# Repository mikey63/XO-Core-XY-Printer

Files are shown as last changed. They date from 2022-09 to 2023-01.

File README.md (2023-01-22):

# XO-Core-XY-Printer
Compact Enclosed Core XY 3D printer with design elements from multiple open-source printers
This printer is based on the Voron V.0, Tiny M, and SnakeOil XY printers.  It's basically a larger version of a Voron V.0 using 2020 extrusions, and has a 220x220x200 build volume, but the electronics setup from a Trident.

Uses BTT Octopus for MCU, and a Raspberry Pi for Klipper.

Use the Voron Trident documentation to setup the MCU and Klipper, then use my config and klicky files.  That should get you up and running, and nearly ready to print.  Before printing, make sure to fine tune the clicky dock position.

For more info:
https://www.youtube.com/watch?v=fIn6DrubGhQ

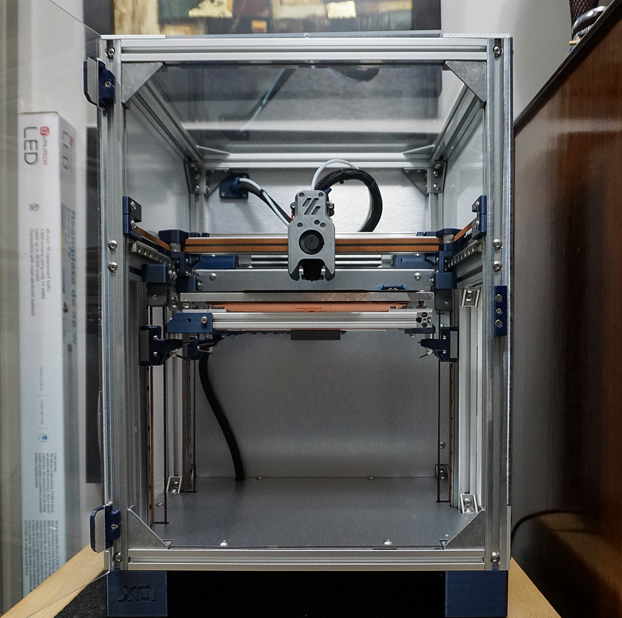
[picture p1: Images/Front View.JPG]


# NOTES

# ***UPDATE 1/21/23!!***

A.  NEW Toolhead!  I am in the process of upgrading to the new Voron V0.2 Mini Stealthburner toolhead!  Of course, I modified it to work with the longer Rapido hotend.  The basic toolhead parts are the same as the voron version, and I changed up the X carriage to match the new bolt pattern.  This means that any V0.2 toolhead will bolt on the carrage, no modified parts are needed like before.  Hopefully, this makes it easier to use the stock voron toolhead, or any iteration meant to work with the voron 0.2 carriage mount.  The Voron team did a great design on this new version, so I removed the original mini-afterburner from the model.  The only changed part on my stealthburner version is the front shroud, and the Rapido hotend mount.  Now that the hotend mount is a separate part, it makes it much easier to assemble, and change hotends!

B. Minor corrections to the CAD model were made.  notably one of the rear bed carrier brackets, and the Z carriage bearing hole was made a tiny bit smaller in hopes for a tighter fit.  

Other than that, there hasn't been much development.  Mostly because the printer has been amazing, and I haven't run into any issues that needed to be addressed.

PREVIOUS NOTES BELOW:

1.  I'm still working on a composite BOM for the major components (like frame parts).  I did not render every fastener, screw, bolt, etc.  I learned fusion360 as a hobby, and just didn't have the time and skill for a professional rendor like that (sorry!)
2.  That said - you will need a few packs of M5 bolts (I used button head M5's), and also some M3 (socket head) bolts.  Also get the corresponding M5 and M3 drop-in T-nuts.  I don't have the exact count on these since I had multiple packs in my stash that I picked from.  Typical M5 variety packs should work, but you may need to get a pack of Just longer M5's, from 20mm-40mm for the few longer pieces you will need.  you'll also need a few 3mm square nuts for the x carriage mount.
3.  I'm using 20x40mm corner gussets from Framingtech.com https://www.framingtech.com/20-x-40-gusset at the inside corners of the frame. These are pretty pricey, but they are very well made.  You can substitute these with some regular corner brackets if you want to save some money.
4.  for motors - X and Y can use any typical Nema 17.  I used 48mm Motors.  For the Z motors, you will need to use the pre-geared Nema 17s, like these: https://www.amazon.com/gp/product/B00WATUFIG/ref=ppx_yo_dt_b_search_asin_title?ie=UTF8&psc=1   These steppers have a built in 5.18:1 gear ratio.  The config file will have the correct rotation distance in the Z_stepper section for these to work.  The Toolhead uses a 36mm round Nema 14 that is typical to other small extruders, like the orbiter or mini-sherpa.
5.  The tool head is a modified V0 tool head.  it has longer fan ducts for a rapido hotend, and it's 3mm thicker on the front side to account for a 30x30x10mm fan in lieu of a 30x30x7mm fan that is the standard for the V0.  You can use the stock V0 in it's place, or any one of the other iterations and mods for this toolhead.
6.  The X carriage is a little different than the standard voron carriage, as it has accomodations for the clicky probe mount, and also a custom backplate behind the nema motor for wire management.  These extra parts can be easily modified to account for different hotends and wiring setups.  right now most of the parts have captured nuts, but I will be working on a version with heatset inserts for a future update.  Some of the captured nuts I'm using at the sides of the mount are 3mm square nuts.  again, this may be updated to heat inserts sometime in the future, when I get around to buying some more.
7.  The bed frame uses 1515 extrusions and matching corner brackets that I had custom laser cut.  There is a dxf file for these triangular brackets that you can send to a 3rd party laser cutting service to have made.  I had them made at the same time I had the side panels cut, and used SendCutSend, located in the USA.  You can probably aso 3d print these parts as well.
8.  This IS a work in progress for the most part.  If you find any issues, or have questions, please let me know, and I'll do my best to update the files.

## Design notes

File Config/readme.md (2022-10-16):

To setup your klicky probe, make a directory in your Klipper "config" folder called "klicky" Then copy these files into that folder. be sure to check out klicky documentation for more information: https://github.com/jlas1/Klicky-Probe

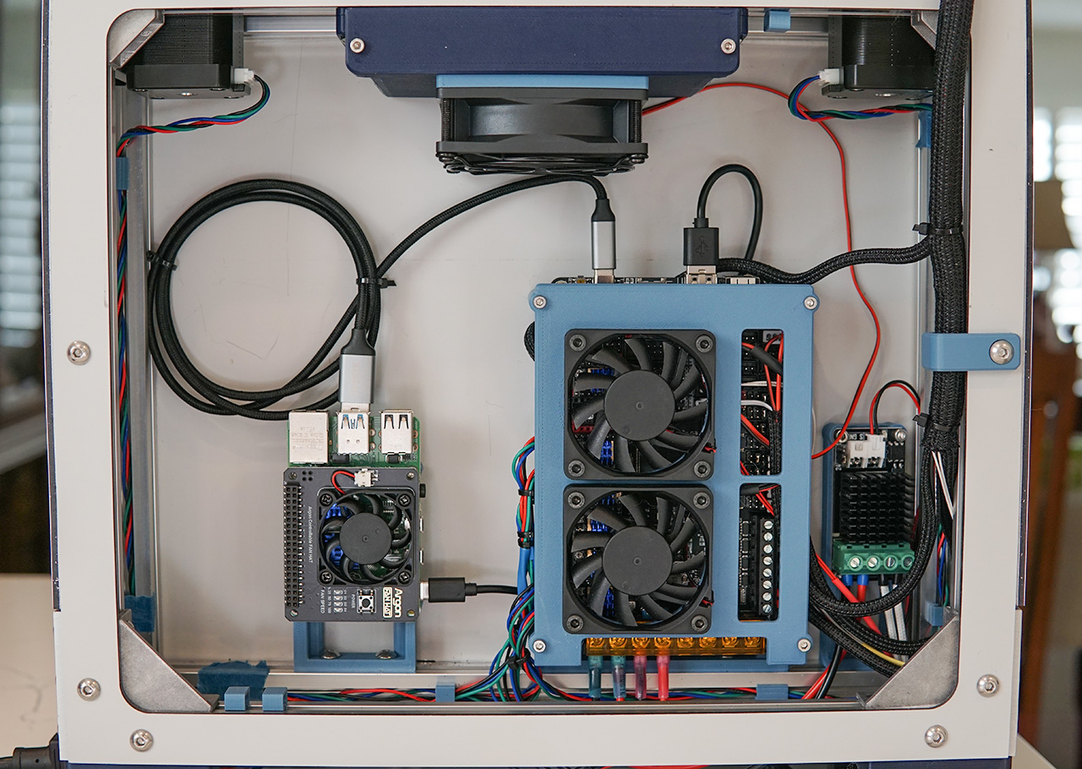
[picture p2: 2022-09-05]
Images/Rear Panel Electronics.JPG

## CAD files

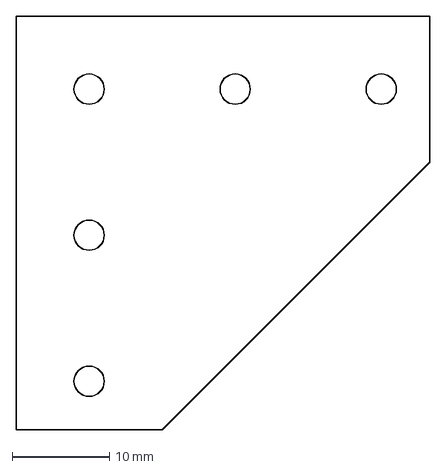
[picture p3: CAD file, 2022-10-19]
CAD Assembly/1515 Corner Plate for Bed Frame.dxf
42.5 x 42.5 mm

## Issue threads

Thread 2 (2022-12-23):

[Suggestion] Control your RPI fan hat with macros

thiagolocatelli, 2022-12-23:
You can control the fan speed on your fan hat by using macros and I2C. Just install the gcode shell command klipper plugin (manually or via Kiuah), enable I2C via `raspi-config` and then use there

```
[gcode_shell_command rpi_fan_50]
command: i2cset -y 1 0x01a 0x32
timeout: 30.
verbose: True

[gcode_shell_command rpi_fan_25]
command: i2cset -y 1 0x01a 0x19
timeout: 30.
verbose: True

[gcode_macro rpi_fan_50]
gcode:
    RUN_SHELL_COMMAND CMD=rpi_fan_50

[gcode_macro rpi_fan_25]
gcode:
    RUN_SHELL_COMMAND CMD=rpi_fan_25
```

mikey63, 2022-12-23:
Awesome, Thank you!  I'll give this a shot.

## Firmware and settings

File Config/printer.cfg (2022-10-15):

# This file contains common pin mappings for the BigTreeTech Octopus V1.
# To use this config, the firmware should be compiled for the STM32F446 with a "32KiB bootloader"
# Enable "extra low-level configuration options" and select the "12MHz crystal" as clock reference

# after running "make", copy the generated "klipper/out/klipper.bin" file to a
# file named "firmware.bin" on an SD card and then restart the OctoPus with that SD card.

# See docs/Config_Reference.md for a description of parameters.

## Voron Design Trident 250/300/350mm BigTreeTech OctoPus V1 TMC2209 UART config

## *** THINGS TO CHANGE/CHECK: ***
## MCU paths                            [mcu] section
## Thermistor types                     [extruder] and [heater_bed] sections - See https://www.klipper3d.org/Config_Reference.html#common-thermistors for common thermistor types
## Leadscrew Rotation Distance          [stepper_z], [stepper_z1], [stepper_z2]
## Z Endstop Switch location            [safe_z_home] section
## Z Endstop Switch  offset for Z0      [stepper_z] section
## PID tune                             [extruder] and [heater_bed] sections
## Probe pin                            [probe] section
## Fine tune E steps                    [extruder] section


[mcu]
##  Obtain definition by "ls -l /dev/serial/by-id/" then unplug to verify
##--------------------------------------------------------------------
serial: /dev/serial/by-id/usb-Klipper_stm32f446xx_370021000F5053424E363620-if00
restart_method: command
##--------------------------------------------------------------------


[include mainsail.cfg]
[include klicky/klicky-probe.cfg]


[printer]
kinematics: corexy
max_velocity: 400 
max_accel: 8000             #Max 4000
max_z_velocity: 18          #Max 15 for 12V TMC Drivers, can increase for 24V
max_z_accel: 350
square_corner_velocity: 5.0

[firmware_retraction]
retract_length: 1.2
retract_speed: 55
unretract_extra_length: 0
unretract_speed: 45

#####################################################################
#   X/Y Stepper Settings
#####################################################################

##  B Stepper - Left
##  Connected to MOTOR_0
##  Endstop connected to DIAG_0
[stepper_x]
step_pin: PF13
dir_pin: PF12
enable_pin: !PF14
rotation_distance: 40
microsteps: 32
full_steps_per_rotation: 200  #set to 400 for 0.9 degree stepper
#endstop_pin: PG6   #Not needed for sensorless homing?
endstop_pin: tmc2209_stepper_x:virtual_endstop
#position_min: 0    #Not needed for sensorless homing?
position_max: 210
position_endstop: 0
##--------------------------------------------------------------------
homing_speed: 90      #Max 100
homing_retract_dist: 0
homing_positive_dir: false

##  Make sure to update below for your relevant driver (2208 or 2209)
[tmc2209 stepper_x]
uart_pin: PC4
diag_pin: ^PG6
interpolate: False
run_current: 1.0
sense_resistor: 0.110
stealthchop_threshold: 0
driver_SGTHRS:  115

##  A Stepper - Right
##  Connected to MOTOR_1
##  Endstop connected to DIAG_1
[stepper_y]
step_pin: PG0
dir_pin: PG1
enable_pin: !PF15
rotation_distance: 40
microsteps: 32
full_steps_per_rotation: 200  #set to 400 for 0.9 degree stepper
#endstop_pin: PG9
endstop_pin: tmc2209_stepper_y:virtual_endstop
#position_min: 0
position_max: 229
position_endstop: 0
##--------------------------------------------------------------------
homing_speed: 90  #Max 100
homing_retract_dist: 0
homing_positive_dir: false

##  Make sure to update below for your relevant driver (2208 or 2209)
[tmc2209 stepper_y]
uart_pin: PD11
diag_pin: ^PG9
interpolate: False
run_current: 1.0
sense_resistor: 0.110
stealthchop_threshold: 0
driver_SGTHRS:  115
 
#####################################################################
#   Z Stepper Settings
#####################################################################

##  Z0 Stepper - Front Left
##  Connected to MOTOR_2
##  Endstop connected to DIAG_2
[stepper_z]
step_pin: PF11
dir_pin: PG3
enable_pin: !PG5
# Rotation Distance for TR8x8 = 8, TR8x4 = 4, TR8x2 = 2
rotation_distance: 7.75    
microsteps: 32
#endstop_pin: PG10
endstop_pin: probe:z_virtual_endstop
##  Z-position of nozzle (in mm) to z-endstop trigger point relative to print surface (Z0)
##  (+) value = endstop above Z0, (-) value = endstop below
##  Increasing position_endstop brings nozzle closer to the bed
##  After you run Z_ENDSTOP_CALIBRATE, position_endstop will be stored at the very end of your config
#position_endstop: 0.125
## All builds use same Max Z
position_max: 190
position_min: -2.5
homing_speed: 11.0 # Leadscrews are slower than 2.4, 10 is a recommended max.
second_homing_speed: 3
homing_retract_dist: 3

##  Make sure to update below for your relevant driver (2208 or 2209)
[tmc2209 stepper_z]
uart_pin: PC6
interpolate: False
run_current: 0.6
sense_resistor: 0.110
stealthchop_threshold: 999

##  Z1 Stepper - Rear Center
##  Connected to MOTOR_3
[stepper_z1]
step_pin: PG4
dir_pin: PC1
enable_pin: !PA0
# Rotation Distance for TR8x8 = 8, TR8x4 = 4, TR8x2 = 2
rotation_distance: 7.75
microsteps: 32

##  Make sure to update below for your relevant driver (2208 or 2209)
[tmc2209 stepper_z1]
uart_pin: PC7
interpolate: False
run_current: 0.6
sense_resistor: 0.110
stealthchop_threshold: 999

##  Z2 Stepper - Front Right
##  Connected to MOTOR_4
[stepper_z2]
step_pin: PF9
dir_pin: PF10
enable_pin: !PG2
# Rotation Distance for TR8x8 = 8, TR8x4 = 4, TR8x2 = 2
rotation_distance: 7.75 
microsteps: 32

##  Make sure to update below for your relevant driver (2208 or 2209)
[tmc2209 stepper_z2]
uart_pin: PF2
interpolate: False
run_current: 0.6
sense_resistor: 0.110
stealthchop_threshold: 999


#####################################################################
#   Extruder
#####################################################################

#   Connected to MOTOR_6
#   Heater - HE0
#   Thermistor - T0
[extruder]
step_pin: PE2
dir_pin: !PE3
enable_pin: !PD4
##  Update value below when you perform extruder calibration
##  If you ask for 100mm of filament, but in reality it is 98mm:
##  rotation_distance = <previous_rotation_distance> * <actual_extrude_distance> / 100
rotation_distance: 4.59   #Bondtech 5mm Drive Gears
##  Update Gear Ratio depending on your Extruder Type
##  Use 50:17 for Afterburner/Clockwork (BMG Gear Ratio)
##  Use 80:20 for M4, M3.1
#gear_ratio: 50:10               #mini afterburner/mini sherpa gear ratio
microsteps: 32
full_steps_per_rotation: 200    #200 for 1.8 degree, 400 for 0.9 degree
nozzle_diameter: 0.400
filament_diameter: 1.75
heater_pin: PA2
## Check what thermistor type you have. See https://www.klipper3d.org/Config_Reference.html#common-thermistors for common thermistor types.
## Use "Generic 3950" for NTC 100k 3950 thermistors
sensor_type: Generic 3950
sensor_pin: PF4
min_temp: 10
max_temp: 275
max_power: 1.0
min_extrude_temp: 170
#control = pid
#pid_kp = 26.213
#pid_ki = 1.304
#pid_kd = 131.721

max_extrude_only_distance: 500.0
#Maximum length (in mm of raw filament) that a retraction or extrude-only move may have. 
#If a retraction or extrude-only move requests a distance greater than this value it will 
#cause an error to be returned. The default is 50mm.

##  Try to keep pressure_advance below 1.0
pressure_advance: 0.040
##  Default is 0.040, leave stock
pressure_advance_smooth_time: 0.040

##  E0 on MOTOR6
##  Make sure to update below for your relevant driver (2208 or 2209)
[tmc2209 extruder]
uart_pin: PE1
interpolate: false
run_current: 0.50
sense_resistor: 0.110
stealthchop_threshold: 0


#####################################################################
#   Bed Heater
#####################################################################

[heater_bed]
##  SSR Pin - HE1
##  Thermistor - TB
heater_pin: PA3
## Check what thermistor type you have. See https://www.klipper3d.org/Config_Reference.html#common-thermistors for common thermistor types.
## Use "Generic 3950" for Keenovo heaters
sensor_type: Generic 3950
sensor_pin: PF3
##  Adjust Max Power so your heater doesn't warp your bed. Rule of thumb is 0.4 watts / cm^2 .
max_power: 0.6
min_temp: 0
max_temp: 120
#control: pid
#pid_kp: 58.437
#pid_ki: 2.347
#pid_kd: 363.769

#####################################################################
#   Chamber Temperature Monitoring
#####################################################################

#Not needed if chamber fan is configured below
[temperature_sensor chamber]
sensor_type: Generic 3950
sensor_pin: PF5
min_temp: 0
max_temp: 80
gcode_id: C

#####################################################################
#   Fan and Temperature Control
#####################################################################

[fan]
##  Print Cooling Fan - FAN0
pin: PA8
kick_start_time: 1.0
##  Depending on your fan, you may need to increase this value
##  if your fan will not start. Can change cycle_time (increase)
##  if your fan is not able to slow down effectively
off_below: 0.10
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

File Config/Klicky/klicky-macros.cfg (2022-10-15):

# This macro was provided by discord user Garrettwp to whom i give my thanks for sharing it with me.
# I have tweaked it a lot.
# They are based on the great Annex magprobe dockable probe macros "#Originally developed by Mental,
# modified for better use on K-series printers by RyanG and Trails", kudos to them.
# That macro as since evolved into a klipper plugin that currently is pending inclusion in klipper, 
# more information here, https://github.com/Annex-Engineering/Quickdraw_Probe/tree/main/Klipper_Macros
# User richardjm revised the macro variables and added some functions
# User sporkus added led status notifications
# Thanks to all who helped,
# by standing on the shoulders of giants, lets see if we can see further
#
# the current home for this version is https://github.com/jlas1/Klicky-Probe 

[respond]

[gcode_macro _Probe_Variables]
variable_probe_attached:            False
variable_probe_state:               False
variable_probe_lock:                False
variable_z_endstop_x:               0
variable_z_endstop_y:               0
gcode:


#checks if the variable definitions are up to date
[gcode_macro _klicky_check_variables_version]
gcode:
    {% set version = printer["gcode_macro _User_Variables"].version|default(0) %}

    {% if version != 1 %}
        { action_raise_error("Please update your klicky variables, there are some functionality changes") }
    {% endif %}

[gcode_macro _KlickyDebug]
gcode:
    {% set message  = params.MSG %}
    {% set debug = printer["gcode_macro _User_Variables"].debug|default(False) %}
    
    {% if debug %}
        { action_respond_info(message) }
    {% endif %}    


[gcode_macro _exit_point]
gcode:
    {% set function  = 'pre_' ~ params.FUNCTION %}
    {% set move  = params.MOVE|default(0) %}
    {% set speed = printer["gcode_macro _User_Variables"].travel_speed %}

    # mandatory to save the new safe position
    M400
    SET_VELOCITY_LIMIT ACCEL={printer.configfile.settings.printer.max_accel}
    SET_VELOCITY_LIMIT ACCEL_TO_DECEL={printer.configfile.settings.printer.max_accel_to_decel}
    RESTORE_GCODE_STATE NAME={function} MOVE={move} MOVE_SPEED={speed}


[gcode_macro _entry_point]
gcode:
    {% set function  = 'pre_' ~ params.FUNCTION %}
    {% set move_accel = printer["gcode_macro _User_Variables"].move_accel|default(1000) %}
    # mandatory to save the new safe position
    M400
    SAVE_GCODE_STATE NAME={function}
    # removes the Z offset for better bed based docking
    SET_GCODE_OFFSET Z=0
    # all the macros initially assume absolute positioning
    G90
    # set a safe(sane) Acceleration
    SET_VELOCITY_LIMIT ACCEL={move_accel}

[gcode_macro _Homing_Variables]
gcode:
    {% set reset  = params.RESET|default(0) %}
    {% if reset %}
        SET_GCODE_VARIABLE MACRO=_Probe_Variables VARIABLE=probe_lock VALUE={ False }
    {% endif %}

##########################
# Attach probe and lock it
[gcode_macro Attach_Probe_Lock]
description: Attaches Klicky Probe, can only be docked after unlocking
gcode:
    Attach_Probe
    _Probe_Lock

########################
# Dock probe and lock it
[gcode_macro Dock_Probe_Unlock]
description: Docks Klicky Probe even if it was locked
gcode:
    _Probe_Unlock
    Dock_Probe

##############
# Unlock Probe
[gcode_macro _Probe_Unlock]
description: Unlocks Klicky Probe state
gcode:
    _KlickyDebug msg="_Probe_Lock setting probe_lock variable to False"
    SET_GCODE_VARIABLE MACRO=_Probe_Variables VARIABLE=probe_lock VALUE={ False }

############
# Lock Probe
[gcode_macro _Probe_Lock]
description: Locks Klicky Probe state
gcode:
    _KlickyDebug msg="_Probe_Lock setting probe_lock variable to True"
    SET_GCODE_VARIABLE MACRO=_Probe_Variables VARIABLE=probe_lock VALUE={ True }

###################
# Klicky Dock Servo Deploy

[gcode_macro _DeployKlickyDock]
description: Deploys Klicky servo-controlled dock
gcode:
    {% set enable_dock_servo = printer["gcode_macro _User_Variables"].enable_dock_servo|default(False) %}
    {% set servo_delay = printer["gcode_macro _User_Variables"].servo_delay|default(1000) %}
    {% set servo_name = printer["gcode_macro _User_Variables"].servo_name %}
    {% set servo_deploy = printer["gcode_macro _User_Variables"].servo_deploy|default(360) %}

    #wait for all the moves to complete
    M400
    {% if enable_dock_servo != False %}
        _KlickyDebug msg="_DeployKlickyDock Klicky servo configuration enabled"
        {% if servo_deploy == 360 %}
            { action_raise_error("Klicky: servo active on klicky-variables, but no servo deploy angle specified") }
        {% endif %}
        _KlickyDebug msg="_DeployKlickyDock SET_SERVO SERVO={servo_name|string} ANGLE={servo_deploy|int}"
        SET_SERVO SERVO={servo_name|string} ANGLE={servo_deploy|int}
        M400
        G4 P{servo_delay|int}
        _KlickyDebug msg="_DeployKlickyDock SET_SERVO SERVO={servo_name|string} WIDTH=0"
        SET_SERVO SERVO={servo_name|string} WIDTH=0
    {% elif printer["gcode_macro _DeployDock"] is defined %}
        _KlickyDebug msg="_DeployKlickyDock calling _DeployDock"	
        _DeployDock
    {% endif %}

####################
# Dock Servo Retract

[gcode_macro _RetractKlickyDock]
description: Retracts Klicky servo-controlled dock
gcode:
    {% set enable_dock_servo = printer["gcode_macro _User_Variables"].enable_dock_servo|default(False) %}
    {% set servo_delay = printer["gcode_macro _User_Variables"].servo_delay|default(1000) %}
    {% set servo_name = printer["gcode_macro _User_Variables"].servo_name %}
    {% set servo_retract = printer["gcode_macro _User_Variables"].servo_retract|default(360) %}
    
    #wait for all the moves to complete
    M400
    {% if enable_dock_servo != False %}
        _KlickyDebug msg="_RetractKlickyDock Klicky servo configuration enabled"
        {% if servo_retract == 360 %}
            { action_raise_error("Klicky: servo active on klicky-variables, but no servo retract angle specified") }
        {% endif %}
        _KlickyDebug msg="_RetractKlickyDock SET_SERVO SERVO={servo_name|string} ANGLE={servo_retract|int}"
        SET_SERVO SERVO={servo_name|string} ANGLE={servo_retract|int}
        M400
        G4 P{servo_delay|int}
        _KlickyDebug msg="_RetractKlickyDock SET_SERVO SERVO={servo_name|string} WIDTH=0"
        SET_SERVO SERVO={servo_name|string} WIDTH=0
    {% elif printer["gcode_macro _RetractDock"] is defined %}
        _KlickyDebug msg="_RetractKlickyDock calling _RetractDock"	
        _RetractDock
    {% endif %}
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

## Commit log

2022-10-15 Add files via upload
    Klipper Config File for XO Printer
    [printer.cfg]
2022-10-15 Add files via upload
    Klicky config files for XO printer.
    Make a folder called "klicky" in your config director, and copy these files into it.
    [klicky-bed-mesh-calibrate.cfg, klicky-macros.cfg, klicky-probe.cfg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]
2023-01-22 January 2023 Update
    New Cad file
